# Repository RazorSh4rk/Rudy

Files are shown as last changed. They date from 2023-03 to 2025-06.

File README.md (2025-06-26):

# Rudy

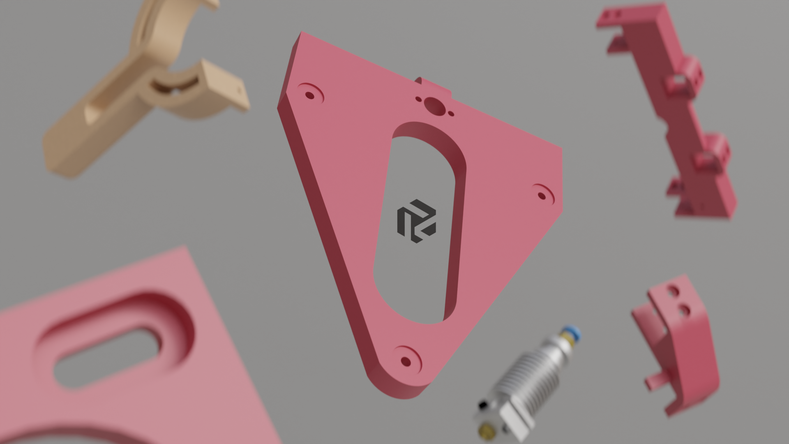
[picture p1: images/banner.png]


## What this _is_

It's a coreXY 3d printer that is

  - cheap
  - reliable
  - small
  - easy to build
  - easy to understand
  - easy to modify
  - open frame

## What this _ain't_

- The fastest printer in the west

- A zero compromise machine

- Something off the shelf

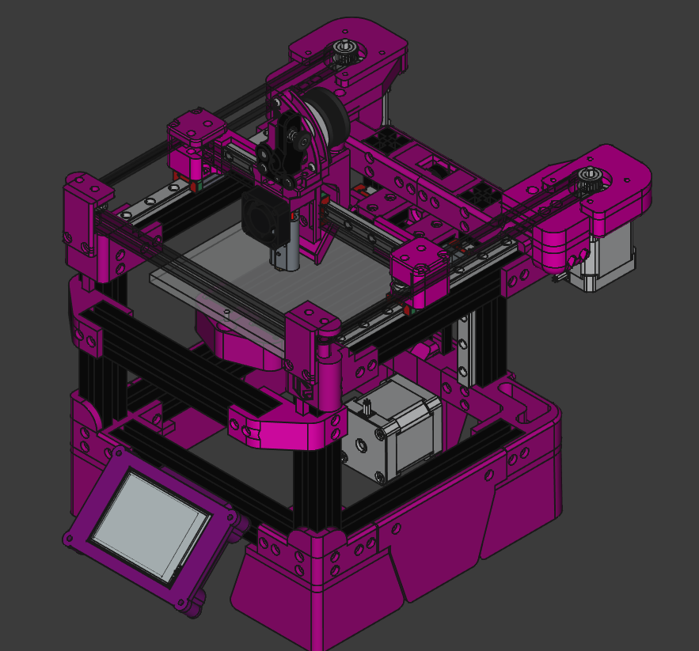
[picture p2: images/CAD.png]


<a href="https://www.youtube.com/watch?v=9IVwhJpB8qE">
    See it in action
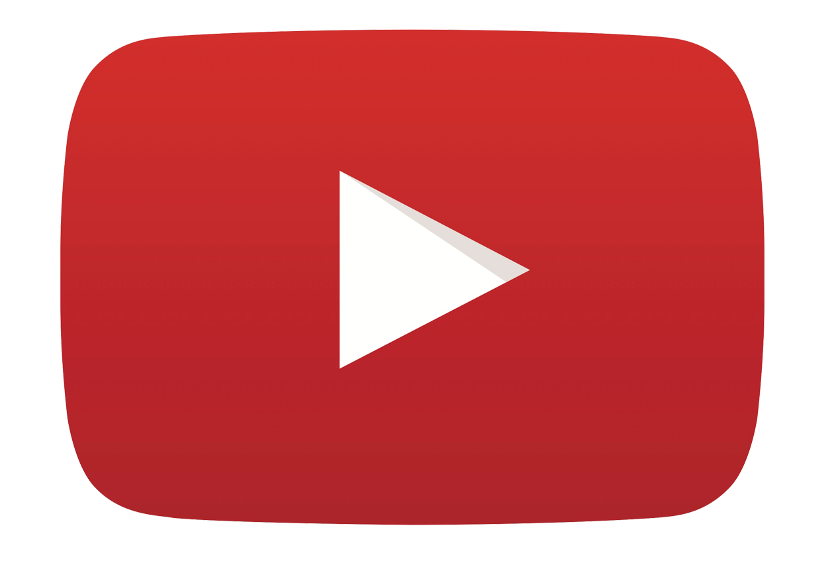
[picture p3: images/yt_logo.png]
    
</a>

<a href="https://discord.com/invite/MBcHGUv2CB">
    Join the discord
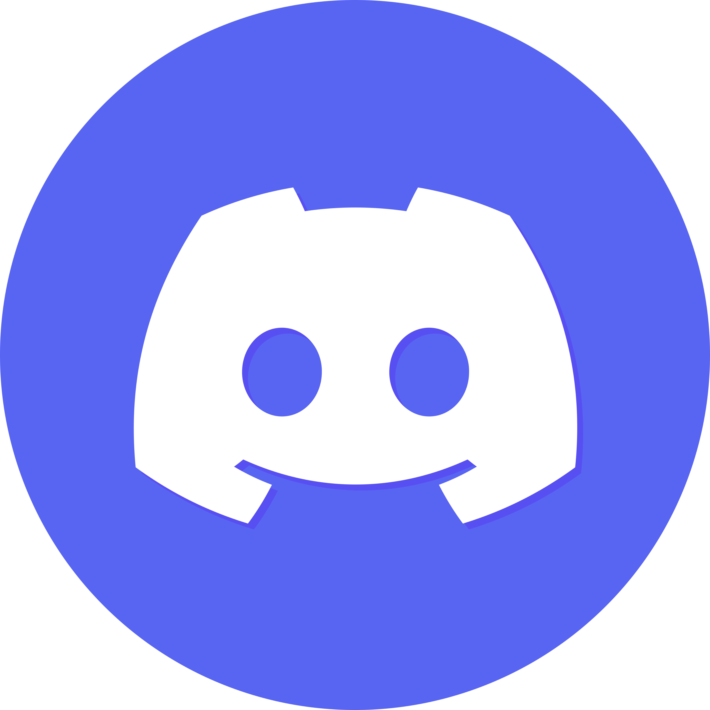
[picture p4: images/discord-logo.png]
    
</a>

---

## GUIDES

 - [Sourcing the parts](./SOURCING_GUIDE.md)
 - [Printing the files](./PRINTING_GUIDE.md)
 - [Choosing a toolhead](./TOOLHEAD.md)
 - [Assembly](./build_guide/assembly.md)

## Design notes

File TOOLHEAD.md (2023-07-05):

# Choosing a toolhead

Rudy uses a front facing mgn9c carriage, so any toolhead that supports that
should work. You ideally want something that's as small on x and y as possible
to not limit travel. If you are using limit switches, you also want to make sure that your toolhead can hit those. 

## Warhead

The Warhead is a custom design specifically made for Rudy. It uses a V6 hotend
with a 3010 fan and a 4010 blower for part cooling. Since it's not strictly a 
part of the Rudy project, it has its own repository and BOM, but if you purchace
the Rudy BOM, you should have enough leftovers to build it too.

Pros:

    - tiny, barely bigger than a V6
    - prints quickly
    - uses standard parts

Cons:

    - in active development
    - the part cooling is okay at best, this is being worked on

[Warhead](https://github.com/RazorSh4rk/warhead)

## Rookery

The Rookery is a very well designed toolhead from Gulsifer on the Rook discord.
It uses the same mounting style as Rudy so it should work too.

Pros:
    
    - much more mature design
    - supports different hotends

Cons:

    - default hardware is very weird, it uses both MK8 and Volcano parts
    - slightly more expensive to source
    - I personally am not convinced of its hotend cooling capability
    - big, it will limit x and z travel

[Rookery](https://www.printables.com/model/381953-rookery-bowden-tool-head)

## DDRudy

DDRudy is a direct drive toolhead custom-designed for the Rudy printer by @skillenmcnot. It is based off the Orbiter v2 extruder and the Trianglelabs CHC Mini hotend.
Other hotend and extruder combinations are possible, although a different extruder may require moving the mounting hole positions in the model.

Pros:
    
    - custom designed for Rudy
    - supports different hotends and common replacement parts
    - excellent cooling performance
    - actively being improved
    - editable model files available

Cons:

    - requires a moderately well-calibrated machine to print properly
    - wider than Warhead, it will limit x travel to 90mm

[DDRudy](https://github.com/skillenmcnot/DDRudy)

# Salad fork

The Salad fork uses the same rail for x, and the modified the mini afterburner
and the mini stealthburner from the voron 0 to fit that. While this is currently
not officially supported on Rudy, i don't see any reason why it couldn't be 
used.

[Salad fork](https://github.com/PrintersForAnts/Salad_Fork/tree/master/STL/Toolhead)

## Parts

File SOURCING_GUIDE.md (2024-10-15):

# BOM

__IMPORTANT__ Rudy was designed with aliexpress in mind. This means that a lot of unevenness, slop, and general China quality is already factored into the printed parts. The frame uses flextures to guarantee squareness, even if the metal parts are bent. Feel free to go for the cheapest listings you can find, or even print parts of the frame yourself (2020 beams are prime candidate for this).

# Frame

| 2020 length | pieces | for what |
| --- | --- | --- |
| 150mm | 6 | top and bottom squares |
| 150mm | 2 | bed carriage | 
| pick a length | 4 | frame Z |

# Z

### for all configs: 

The length of the Z rails is going to be the length of your Z 2020 extrusions _MINUS 50mm_, so if you picked 200mm, then your rails are 150mm, which will give you about 120mm travel.

| Thing | Price | Link |
| --- | --- | --- |
| mgn9c rail (Z length) x2 | - | keep scrolling |

### for leadscrew config:

| Thing | Price | Link |
| --- | --- | --- |
| T8 leadscrew (Z length) P:2mm L:8mm| $2.50 | [link](https://www.aliexpress.com/item/1005002277808736.html?spm=a2g0o.cart.0.0.5c4138daTHlXeg&mp=1) |
| 5x8mm coupler * | $1 | [link](https://www.aliexpress.com/item/32693571252.html?spm=a2g0o.order_detail.order_detail_item.3.2ce7f19cw1xHpY) |

### for belted Z config:

| Thing | Price | Link |
| --- | --- | --- |
| extra belt (3m will have leftover for about 120mm Z) | | |
| extra F695 x2 (there will be enough leftovers) | | |
| one extra gt2 pulley | | keep scrolling |
| M5x35 screw (x40 works too, it will just stick out) | | keep scrolling |

# Common parts

| Thing | Price | Link |
| --- | --- | --- |
| __Hardware__ | | |
| M3 sliding T-nuts x200 (2020 series) | $9 | [link](https://www.aliexpress.com/item/1005002114332413.html?spm=a2g0o.productlist.main.5.3641402fC0BsdY) |
| M3x6 metric screws x200 |  |  |
| M3x8 metric screws x50 (for backup or accessories) |  |  |
| M3x25 (or longer) metric screws x3 |  |  |
| M3x20 x10 |  |  |
| M3x something between 10 and 20 x2 |  |  |
| M2x10 metric screws x2 (optional, hot glue is fine) |  |  |
| M5x40 metric screws x10 |  |  |
| M5 hex nut x2 |  |  |
| M3 (XD5.0XL4.0) inserts x100 (you need 20) | $7.34 | [link](https://www.aliexpress.com/item/4000232858343.html?spm=a2g0o.order_list.order_list_main.107.21ef1802qkslow) |
| __Motion__ |  |  |
| GT2 pulley x2 * | $6.34 | [link](https://www.aliexpress.com/item/32995102911.html?spm=a2g0o.order_list.order_list_main.107.145f1802vFsakT) |
| 6mm GT2 belt x3m | $7.61 | [link](https://www.aliexpress.com/item/902692789.html?spm=a2g0o.order_list.order_list_main.108.145f1802vFsakT) |
| F695 bearing x20 | $23 | [link](https://www.aliexpress.com/item/33001186278.html?spm=a2g0o.order_list.order_list_main.97.145f1802vFsakT) |
| Cheaper F695 (they work fine) | $11 | [link](https://www.aliexpress.com/item/1005004095001000.html) |
| mgn9c rail 150mm x3 * | $30 | [link](https://www.aliexpress.com/item/1005003787436599.html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) |
| 120mm voron 0 bed | $20 | [link](https://www.aliexpress.com/item/1005003229750626.html?spm=a2g0o.order_list.order_list_main.102.21ef1802qkslow) |
| 8x20mm bed springs | $2 | [link](https://www.aliexpress.com/item/1005002971412129.html?spm=a2g0o.productlist.main.1.6c086ad58K77Ue) |
| __Electronics__ |  |  |
| 3x NEMA17 | $25 | [link - pancake](https://www.aliexpress.com/item/1005004708155105.html?spm=a2g0o.order_list.order_list_main.102.145f1802vFsakT) |
| other motor listing (cheaper if you wanna buy 5) | $38 | [link](https://www.aliexpress.com/item/1005001650755939.html?spm=a2g0o.cart.0.0.202b38da9QMU82&mp=1)
| skr pico (or any tmc2209 mainboard) | $20-30 | [pico](https://www.aliexpress.com/item/1005004046648820.html?spm=a2g0o.productlist.main.3.3697bf5bSHKD6H)|
| Orange Pi Zero 2 (or something to run klipper) | $30 | [link](https://www.aliexpress.com/item/1005001823662622.html?spm=a2g0o.productlist.main.1.3a4a1cacYamf5s) |
| Limit switch x1 (MS-1A 13.5) | $1.50 | [link](https://www.aliexpress.com/item/4001033375208.html?) |
| Power supply 24V (~120W) | $20-30 | [link](https://www.aliexpress.com/item/1005004623323483.html?spm=a2g0o.cart.0.0.64b338dahPVvNM&mp=1) |
| Extruder (titan or bmg recommended) | $5-10 | [titan link](https://www.aliexpress.com/item/10000404181488.html?spm=a2g0o.productlist.main.29.219338f9jwvYx4) |

### Extruder notes

If you use bowden, just use whatever extruder you like, a voron m4 or a bmg clone is nice and cheap.

If you want to go bowden, warhead has support for sailfin, and will eventually have support for sherpa micro, so pick either of those (sailfin can be built from a $5 bmg kit)

// BOM subject to change

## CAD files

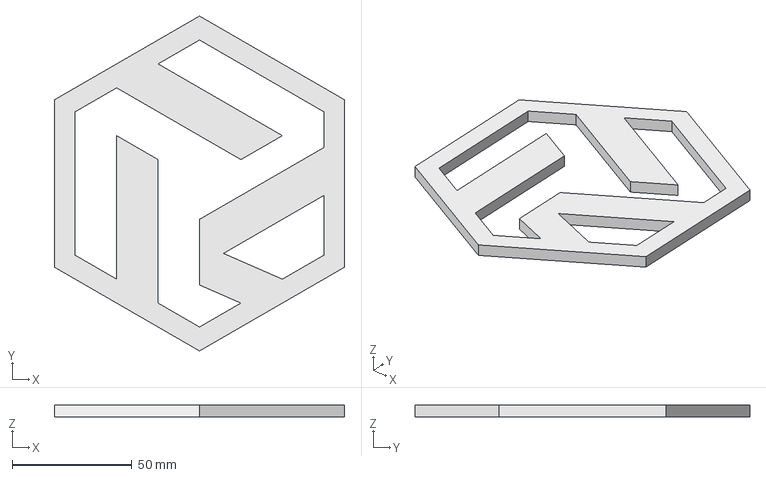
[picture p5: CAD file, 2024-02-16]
logo.step
121.2 x 140.0 x 5.00 mm

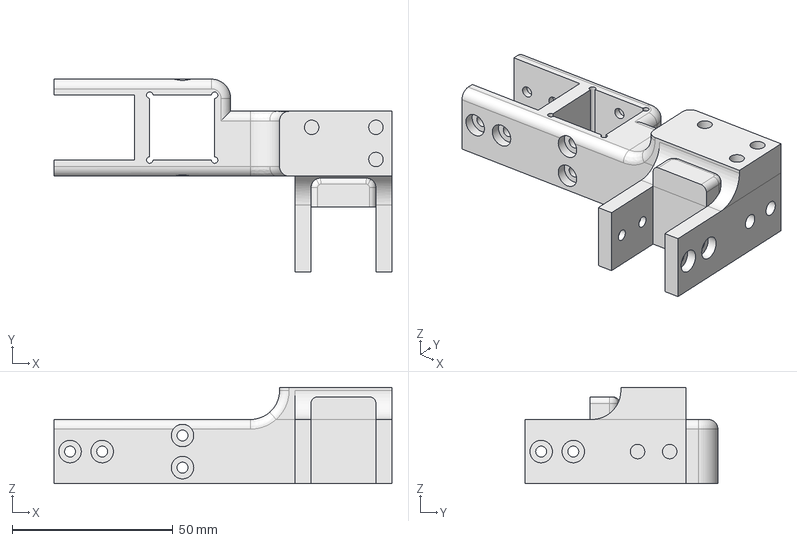
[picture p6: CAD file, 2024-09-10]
refparts/CAD_RR-back_top_right.step
105.2 x 60.0 x 30.0 mm

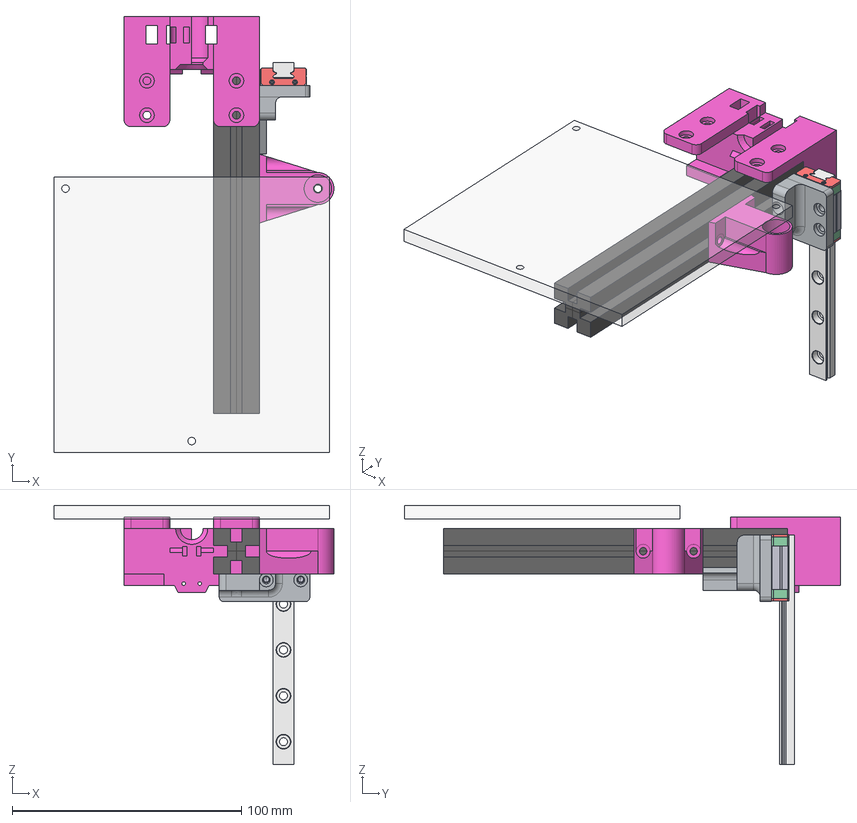
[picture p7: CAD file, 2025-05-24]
STEPs/extras/klicky/reference_z.step
122.0 x 190.0 x 113.0 mm
2020_Y_5
mgn9_z1
MGN9CZFC-Block039
MGN9CZFC-Block040
MGN9CZFC-Block041
MGN9CZFC-Block042
MGN9CZFC-Block043
MGN9CZFC-Block044
MGN9CZFC-Block045
MGN9CZFC-Block046
MGN9CZFC-Block047
Z_reprap_right
Z_reprap_v0_right
V0_bed
Z_reprap_belt

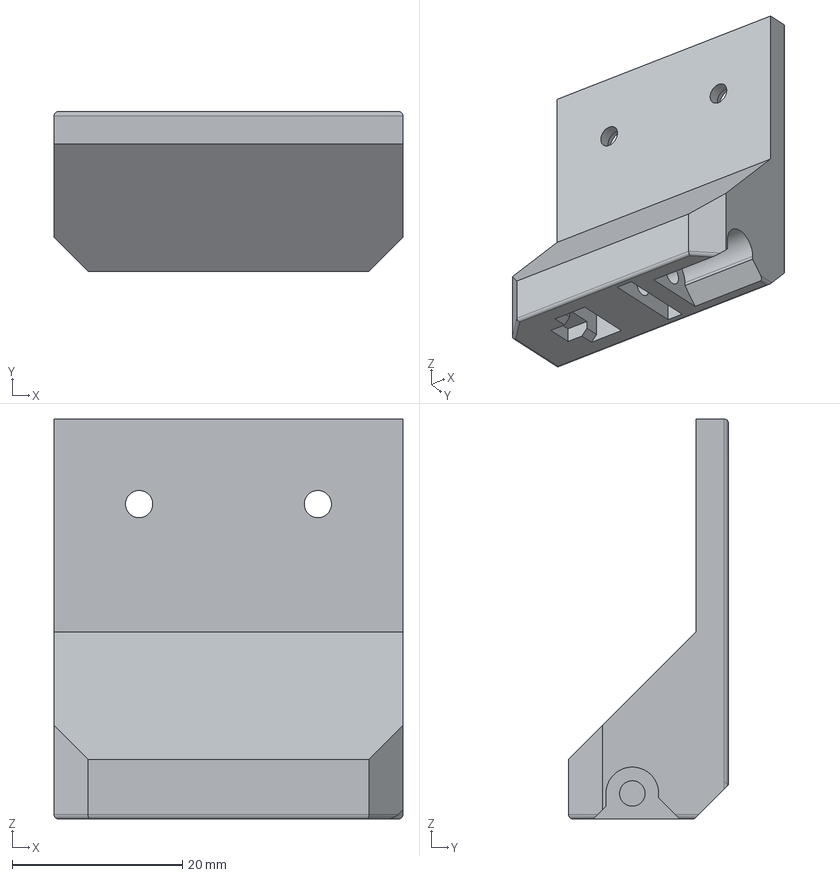
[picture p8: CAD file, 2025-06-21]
STEPs/extras/klicky/sideswipe/servo_mount.step
41.0 x 18.8 x 47.0 mm

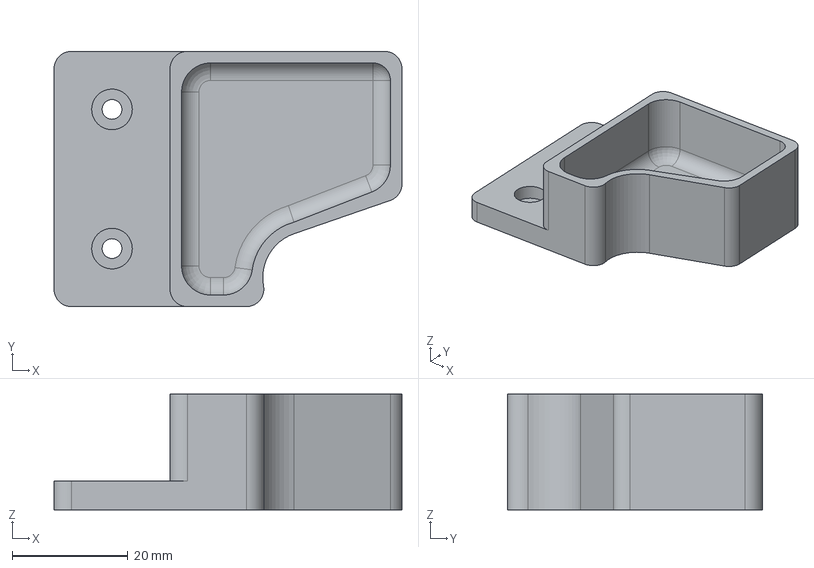
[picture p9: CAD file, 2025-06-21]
STEPs/extras/purge_bucket.step
60.0 x 44.0 x 20.0 mm

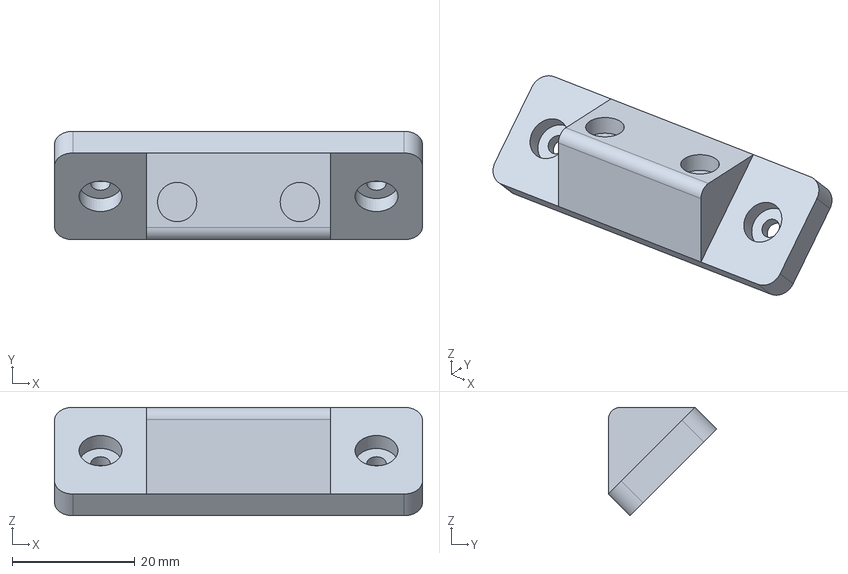
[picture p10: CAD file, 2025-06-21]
STEPs/extras/screen/mount.step
60.0 x 17.7 x 17.7 mm

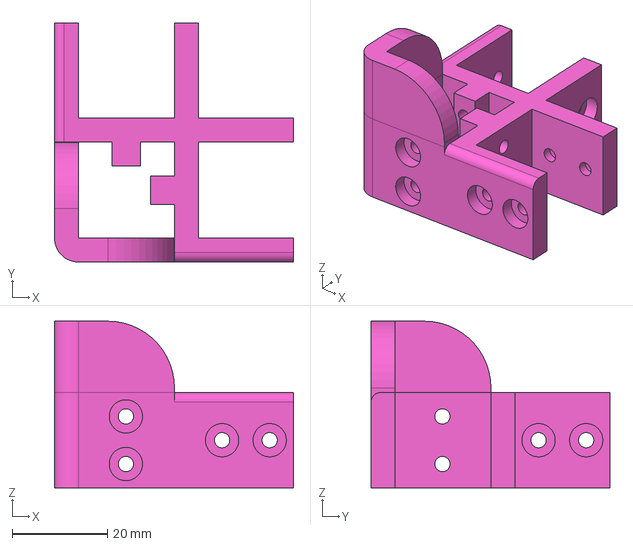
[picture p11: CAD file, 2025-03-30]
STEPs/MK4/frame/bottom/corner_x2.step
50.2 x 50.2 x 35.0 mm

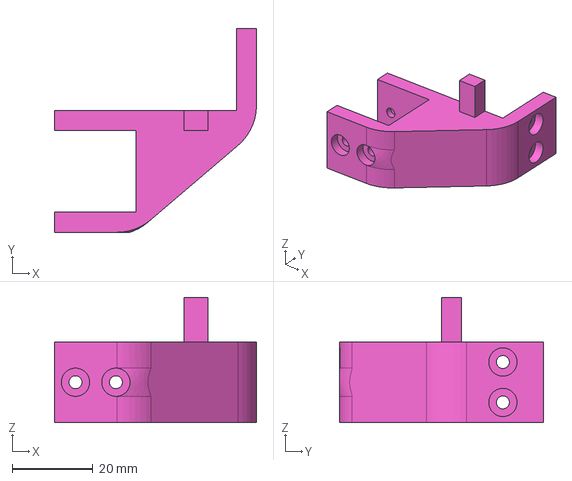
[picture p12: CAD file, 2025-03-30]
STEPs/MK4/frame/top/front_bar_right.step
50.0 x 50.4 x 31.0 mm

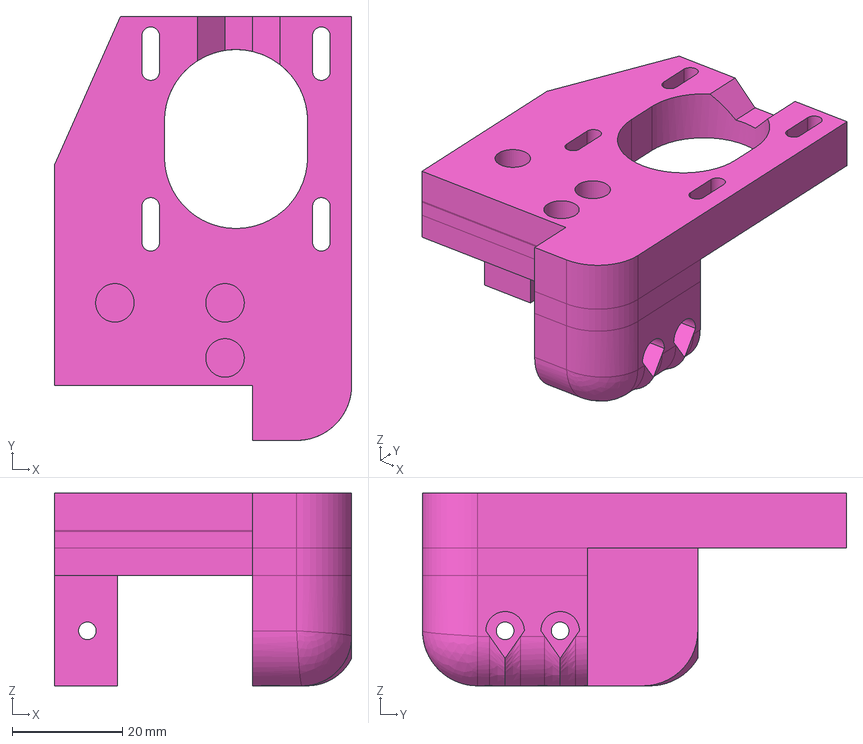
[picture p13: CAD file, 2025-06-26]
STEPs/MK4/motion/XY/motor_mount_right.step
54.0 x 77.0 x 35.0 mm

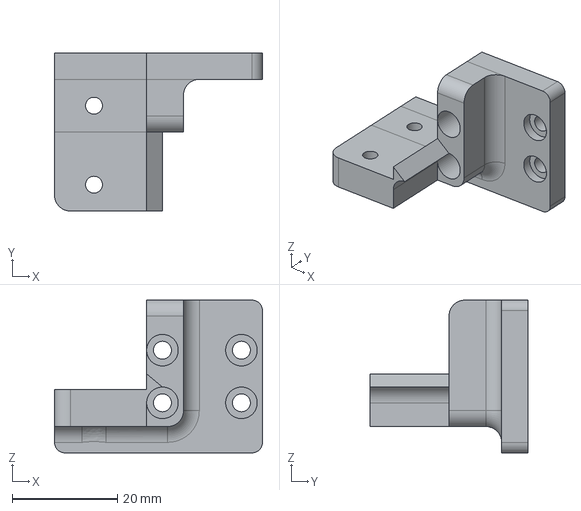
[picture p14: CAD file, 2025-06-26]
STEPs/MK4/motion/Z/bed_carriage_rail_mount_right.step
39.5 x 30.0 x 29.0 mm

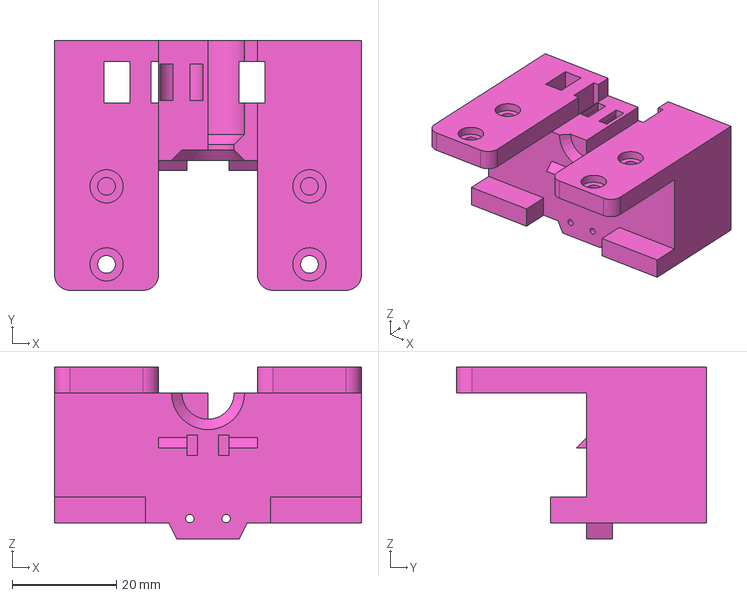
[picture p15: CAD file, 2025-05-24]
STEPs/MK4/motion/Z/belted/belt_attachment.step
59.0 x 48.0 x 33.0 mm

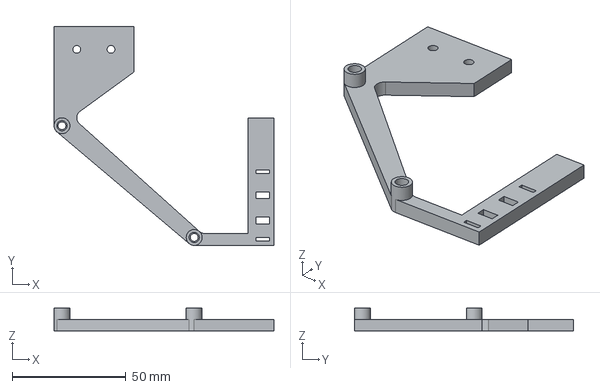
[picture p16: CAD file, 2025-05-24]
STEPs/MK4/mount_stuff/skrpico_mount.step
96.5 x 96.0 x 10.0 mm

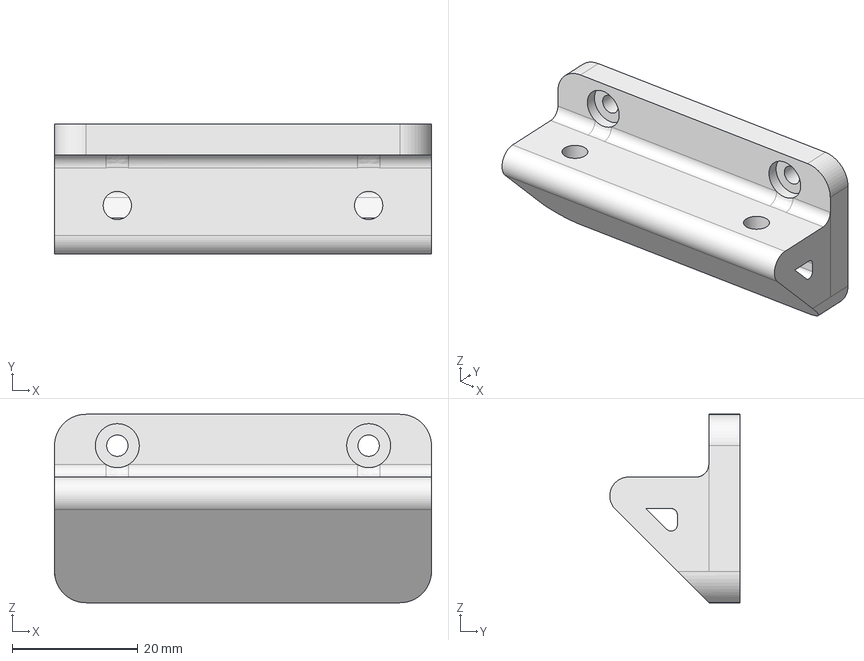
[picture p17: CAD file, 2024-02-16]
STEPs/spool_holder/spool_holder-base.step
60.0 x 20.8 x 30.0 mm

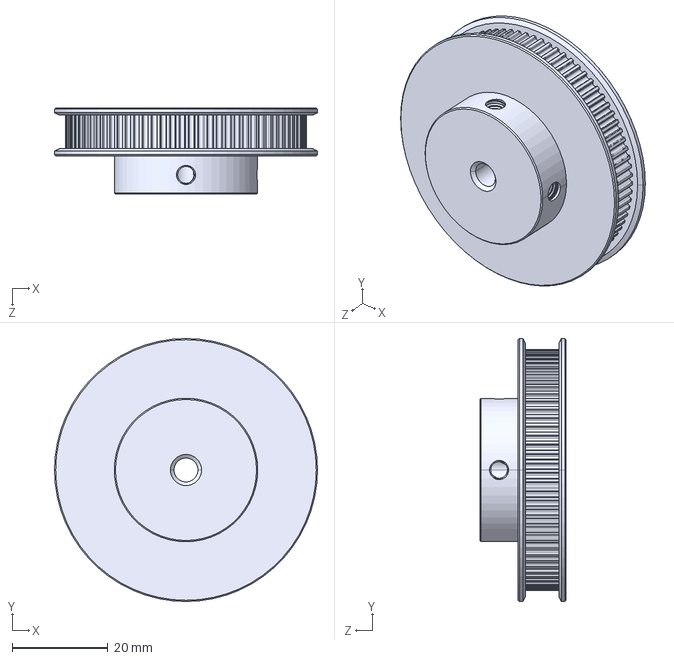
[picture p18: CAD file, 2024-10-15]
things_i_used_for_reference/GT2_80T_5mm_Bore_Pulley.STEP
55.0 x 55.0 x 18.0 mm

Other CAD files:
bed_model_SS.stl
refparts/CAD_RR-back_top_left.step
STEPs/extras/klicky/klicky_cad.FCStd
STEPs/extras/purge_bucket_tall.step
STEPs/MK4/frame/bottom/foot_front_left.step
STEPs/MK4/frame/bottom/foot_front_right.step
STEPs/MK4/frame/bottom/foot_rear_left.step
STEPs/MK4/frame/bottom/foot_rear_right.step
STEPs/MK4/frame/bottom/rear_left.step
STEPs/MK4/frame/bottom/rear_right.step
STEPs/MK4/frame/bottom/skirt_x2_or_x3.step
STEPs/MK4/frame/top/font_bar_left.step
STEPs/MK4/frame/top/front_corner_left.step
STEPs/MK4/frame/top/front_corner_right.step
STEPs/MK4/frame/top/rear_corner_left.step
STEPs/MK4/frame/top/rear_corner_right.step
STEPs/MK4/motion/XY/YCarriage_bottom_left.step
STEPs/MK4/motion/XY/YCarriage_bottom_right.step
STEPs/MK4/motion/XY/YCarriage_top_left.step
STEPs/MK4/motion/XY/YCarriage_top_right.step
STEPs/MK4/motion/XY/belt_tensioner_left.step
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

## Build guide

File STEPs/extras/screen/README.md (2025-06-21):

Uses a 2.8" CYD screen to add a control interface for like $10

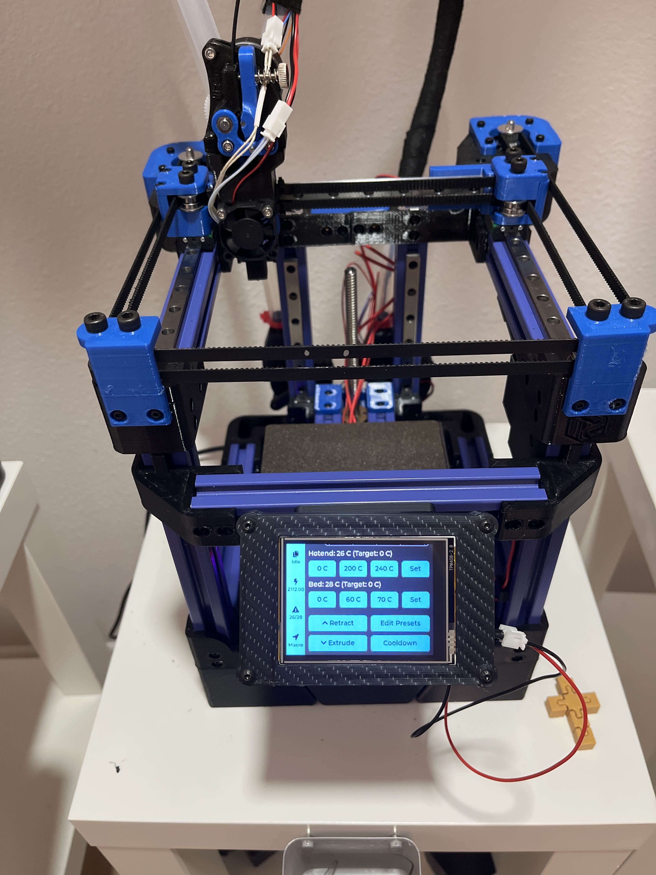
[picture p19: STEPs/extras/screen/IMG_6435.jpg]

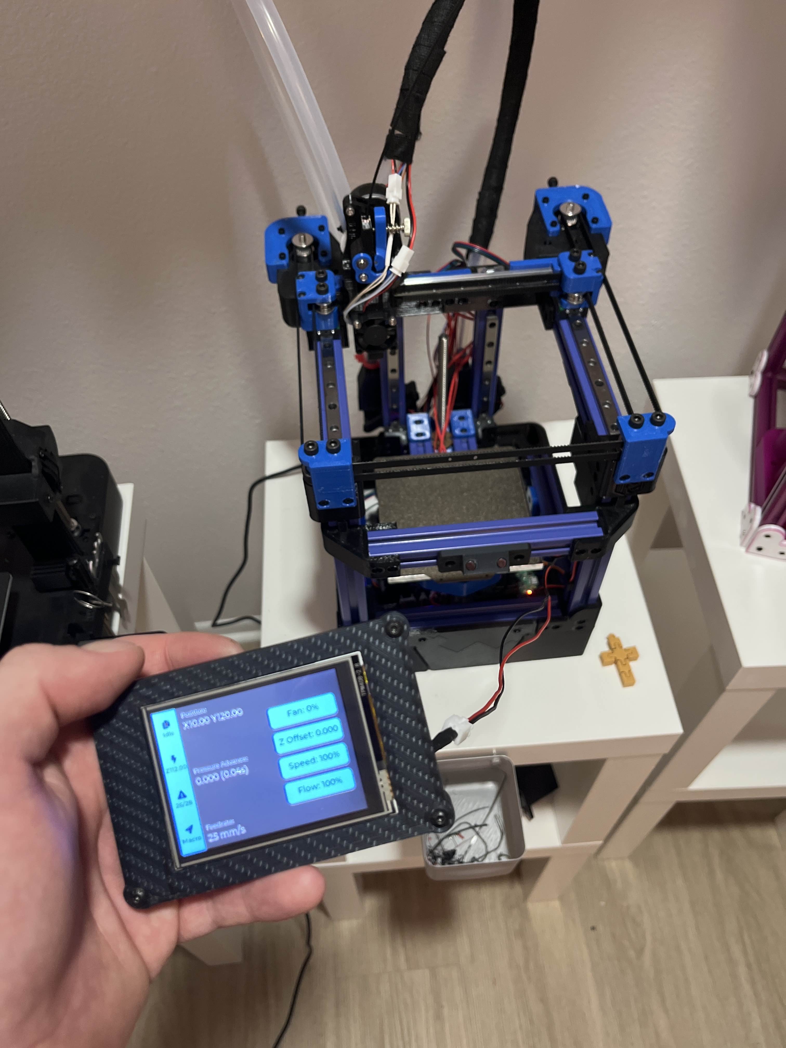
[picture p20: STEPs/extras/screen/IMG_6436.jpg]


Installation: [CYD Klipper](https://github.com/suchmememanyskill/CYD-Klipper)

BOM:

- 5mm OD heated insert x7
- M3x6mm x5
- M3x8? mm x4
- M3 2020 nut x2
- 2.8" CYD (link in the CYD Klipper repo)
- 6x3mm magnet x4

Assembly:

- Flash CYD Klipper
- Add heated inserts to the very obvious holes
- Glue magnets in mount and base
- Supply 5v to the CYD, I used one of the endstop ports, but you can also just use USB

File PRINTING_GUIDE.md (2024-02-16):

# Printing the parts

## Material

Rudy is designed to be easy to print. I used Devil Design PETG for every part. I can't really vouch for PLA working or not, but looking at the design it should be fine for everything but the AB motor mounts. ABS and nylon will most likely work. 

## Slicer

I use superslicer (analogous to prusaslicer), so I can only help with those. If you use cura or simplify3d or whatever, you probably know way more about it than I do anyway.

## Settings

Every part should be printed at 5mm solid walls. This means that if your wall thickness is 1mm, use 5 walls. If it's .8mm (common with .4 nozzles), use 5/.8 = 6.25 (6 or 7) walls. In superslicer you can set this at print settings/vertical_shells. Infill doesn't really matter, i used 18% gyroid. 

Some parts _will_ need suports turned on to make the CAD simpler. Generally "supports on build plate only" should get you most of the way there except the Y carriages where you will need paint-on, or tree support (more on that later).

Every part has a flat surface you can print it on.

## Printing the trickier parts

There are some parts that will need you to tweak settings a bit. Most notorious is gonna be the Y carriages. Use this image to paint on the supports.

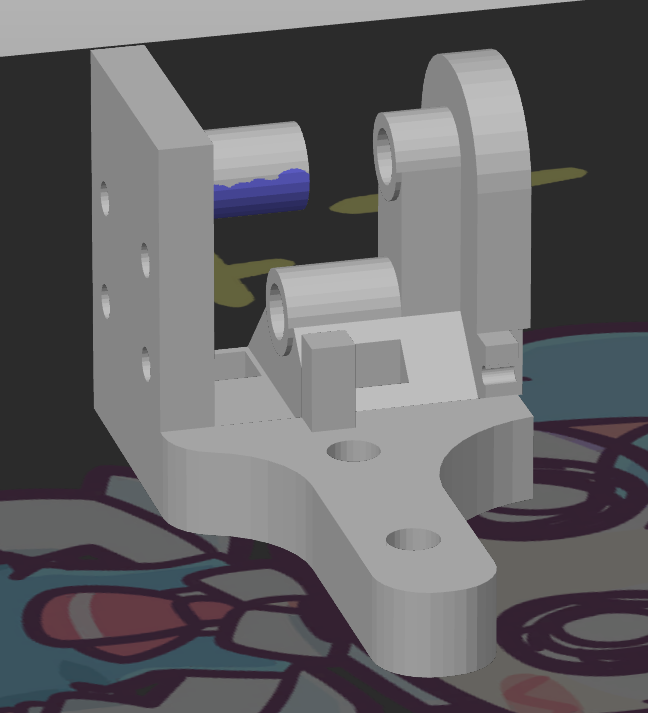
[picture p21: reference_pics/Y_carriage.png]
y


For every other part you want the counterholes to be supported so they don't sag (especially if printing PETG)

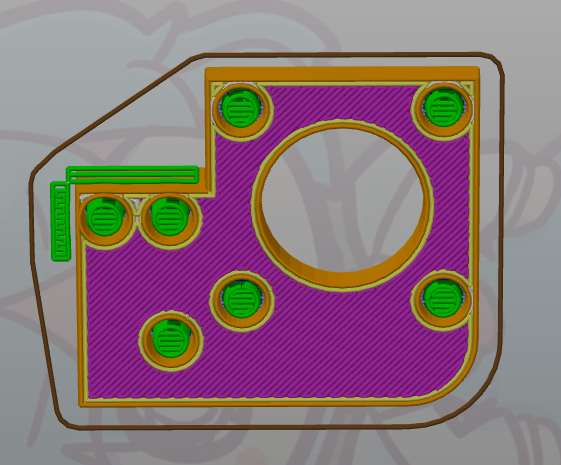
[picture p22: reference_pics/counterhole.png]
support


## Part list

### SCROLL DOWN FOR UPDATED MK2 AND MK3 PARTS

Some parts you will have to mirror in your slicer. To do this in superslicer, right click the imported stl and click "mirror/along X axis". Only place the flat sides down after.

| file | pieces | second one mirrored? |
| --- | --- | --- |
| mgn9_mount_100mm.stl | 2 | no |
| mgn9_mount_150mm.stl | 2 | no |
| back_bottom.stl | 1 |  |
| back_top.stl | 1 |  |
| bed_frame.stl | 1 |  |
| bottom_corner.stl | 2 | no |
| foot_front.stl | 2 | yes |
| `^one mirrored only if you want the logo on the other side` |  |  |
| front_bar_mount.stl | 2 | yes |
| idlerv2-right.stl | 1 | mirror this part!! |
| idlerv2.stl | 1 |  |
| leg_back.stl | 2 | yes |
| motor_mount_A.stl | 2 | yes |
| motor_mount_B_spacer.stl | 1 |  |
| skirt.stl | 3 | no |
| spool_holder.stl | 1 |  |
| top_corner.stl | 2 | no |
| y_carriage_left (Mirror #1).stl | 1 |  |
| y_carriage.stl | 1 |  |
| foot_left_logo.stl | 1 |  |
| leveling_knob.stl | 3/4 | no |
| limit_switch_spacer.stl | 2 | no |
| logo_insert.stl | 1 |  |
| mgn_rail_stopper.stl | 2 | no |

## Part list for MK2

| file change | pieces | second mirrored? |
| --- | --- | --- |
| idlerv2-right.stl -> MK2/idlerv3_right.step| 1 |  |
| idlerv2.stl -> MK2/idlerv3_left.step| 1 |  |
| motor_mount_A.stl -> MK2/motor_mount_left.step | 2 | yes |
| top_corner.stl -> not needed|  |  |
| y_carriage_left -> MK2/y_carriage_v2.step | 1 |  |
| y_carriage.stl -> MK2/y_carriage_v2_right_mirrored.step | 1 |  |
| NEW PARTS |  |  |
| MK2/belt_tensioner_left.step | 2 | yes |

## Part list for MK3

| file change | pieces | second mirrored? |
| --- | --- | --- |
| bed_frame.stl -> not needed |  |  |
| NEW PARTS |  |  |
| MK3/Z_reprap_screw.step | 1 |  |
| MK3/Z_reprap_left.step | 2 | yes |
| MK3/Z_reprap_v0_front | 1 |  |
| MK3/Z_reprap_v0_side | 2 | no |

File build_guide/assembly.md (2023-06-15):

# Assembly

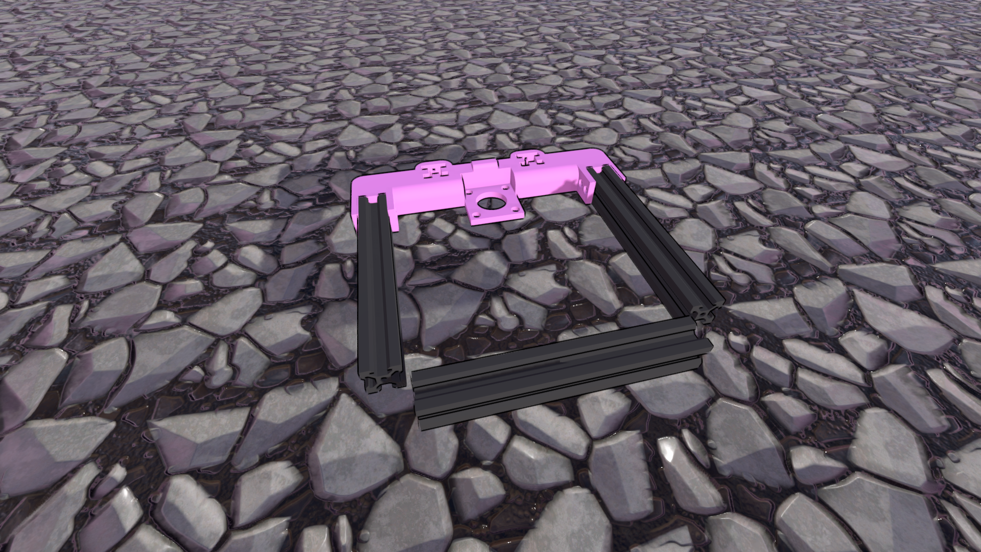
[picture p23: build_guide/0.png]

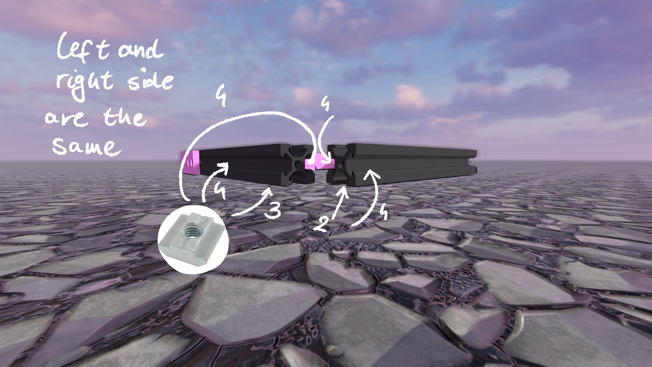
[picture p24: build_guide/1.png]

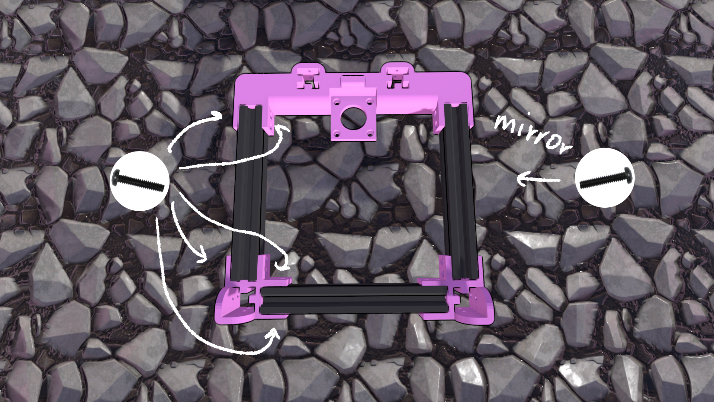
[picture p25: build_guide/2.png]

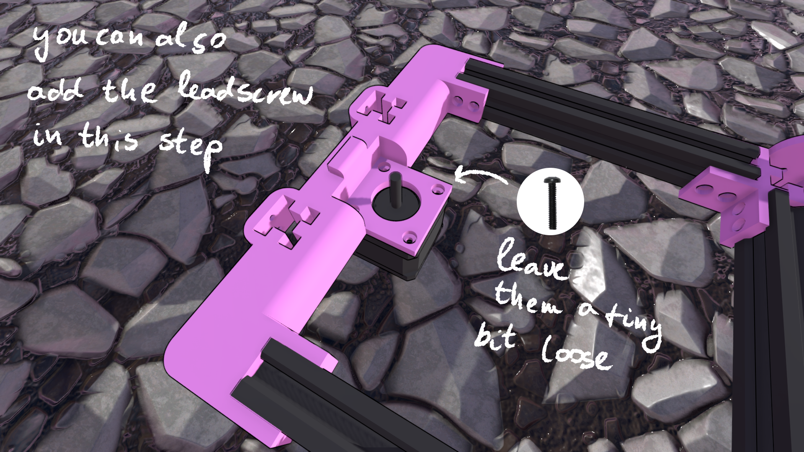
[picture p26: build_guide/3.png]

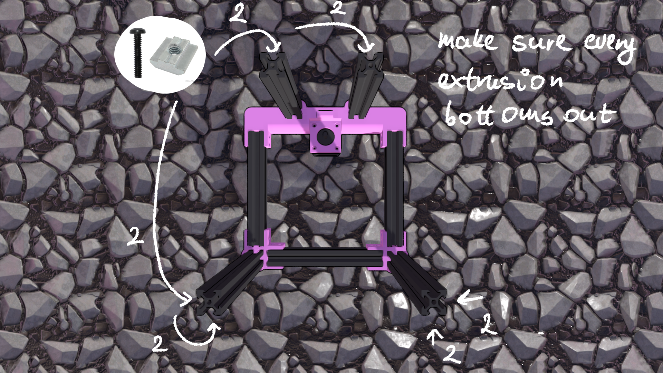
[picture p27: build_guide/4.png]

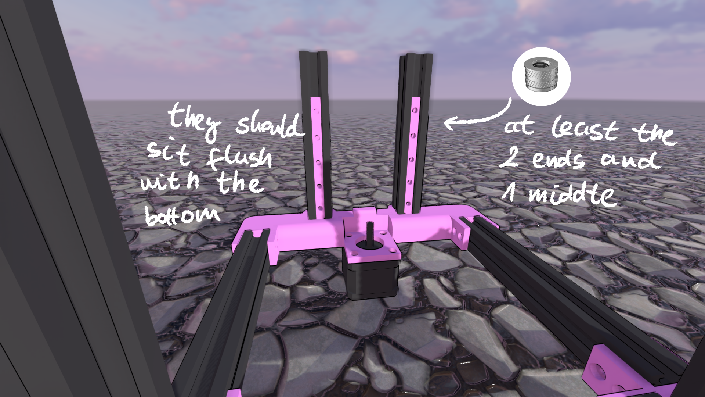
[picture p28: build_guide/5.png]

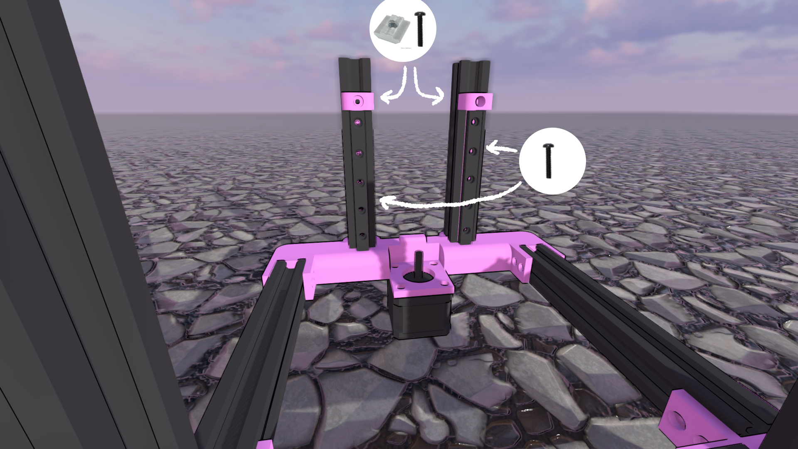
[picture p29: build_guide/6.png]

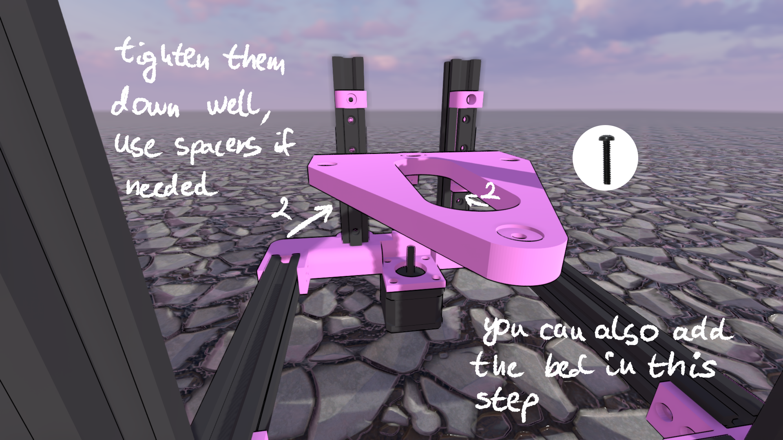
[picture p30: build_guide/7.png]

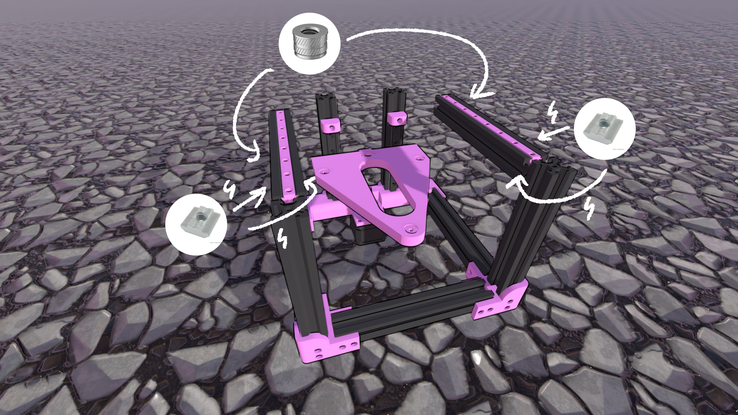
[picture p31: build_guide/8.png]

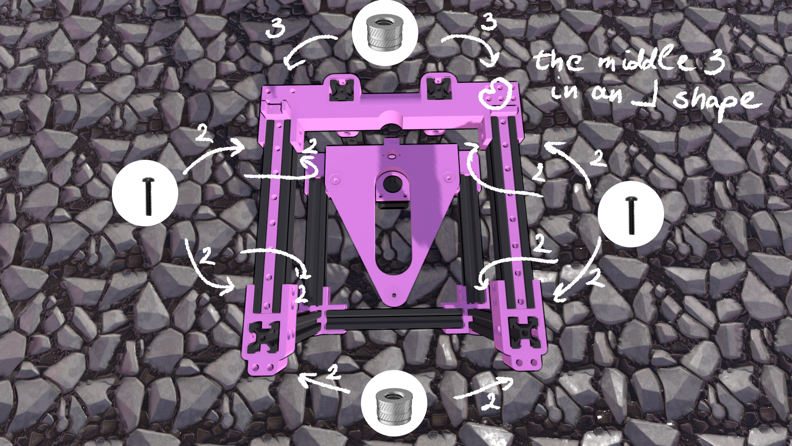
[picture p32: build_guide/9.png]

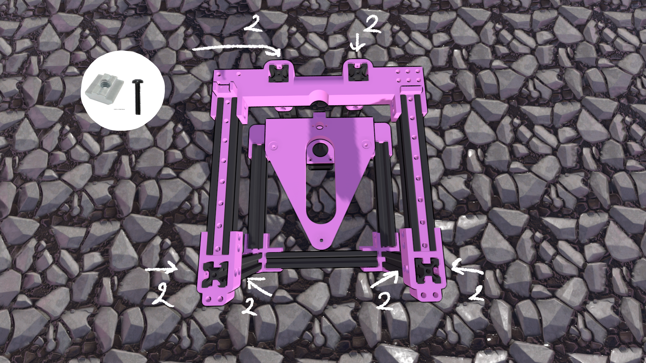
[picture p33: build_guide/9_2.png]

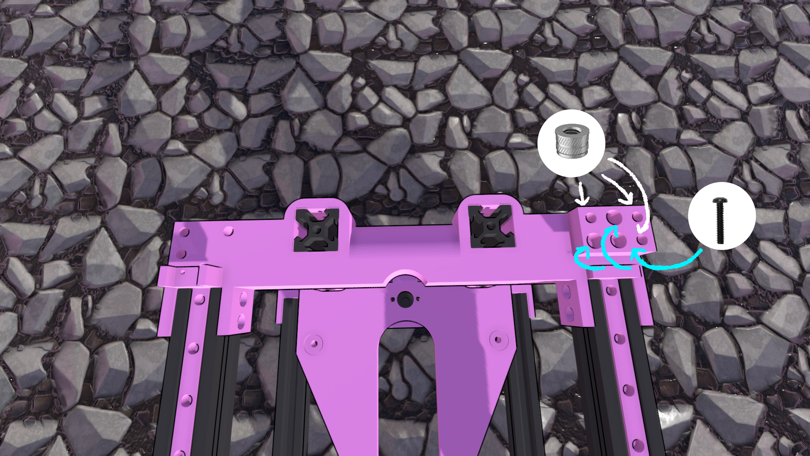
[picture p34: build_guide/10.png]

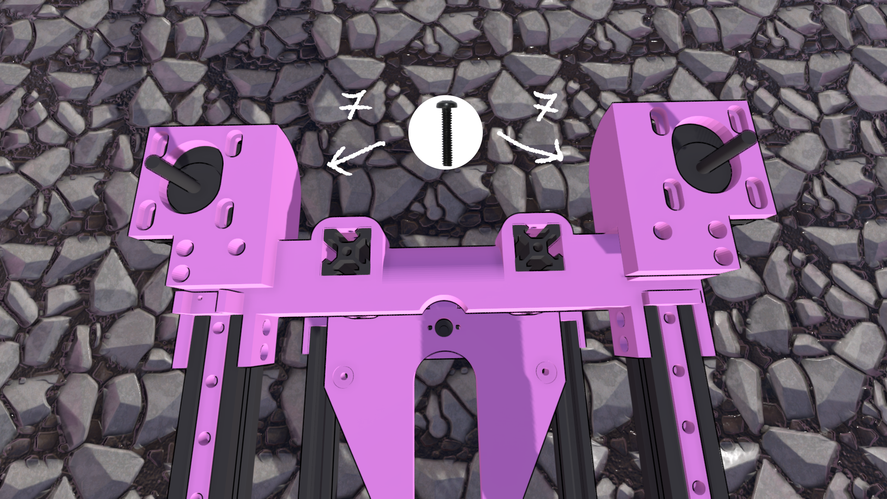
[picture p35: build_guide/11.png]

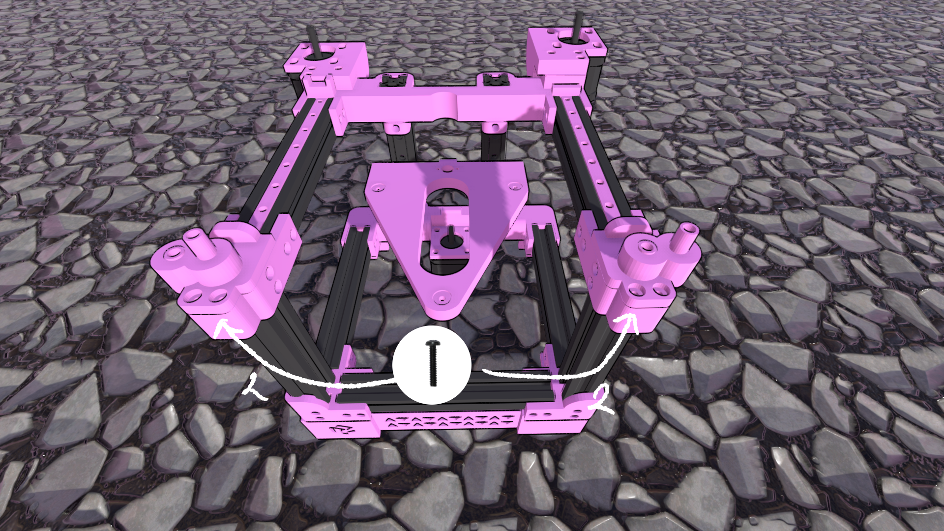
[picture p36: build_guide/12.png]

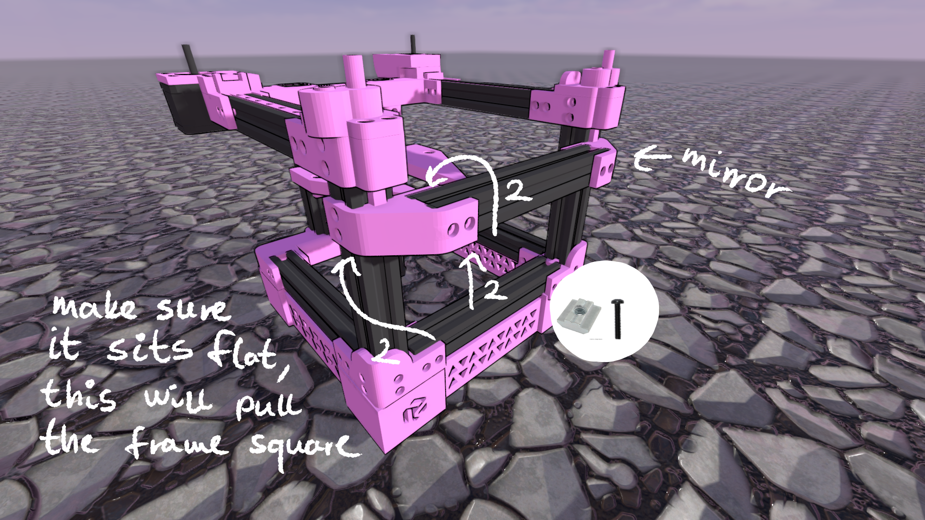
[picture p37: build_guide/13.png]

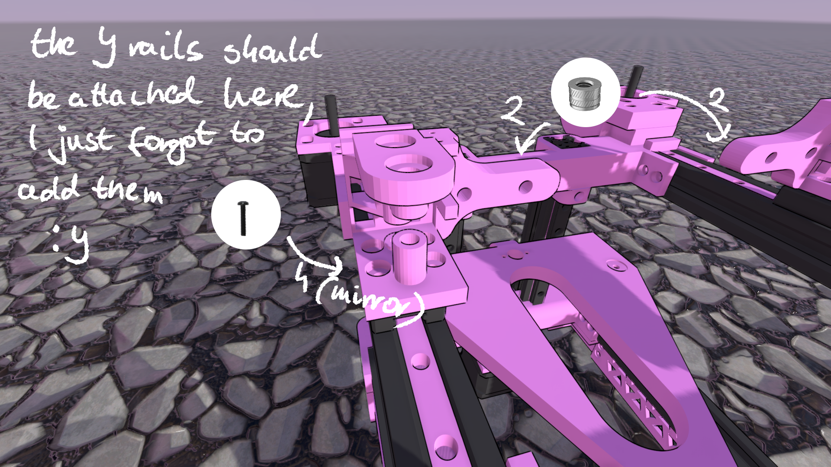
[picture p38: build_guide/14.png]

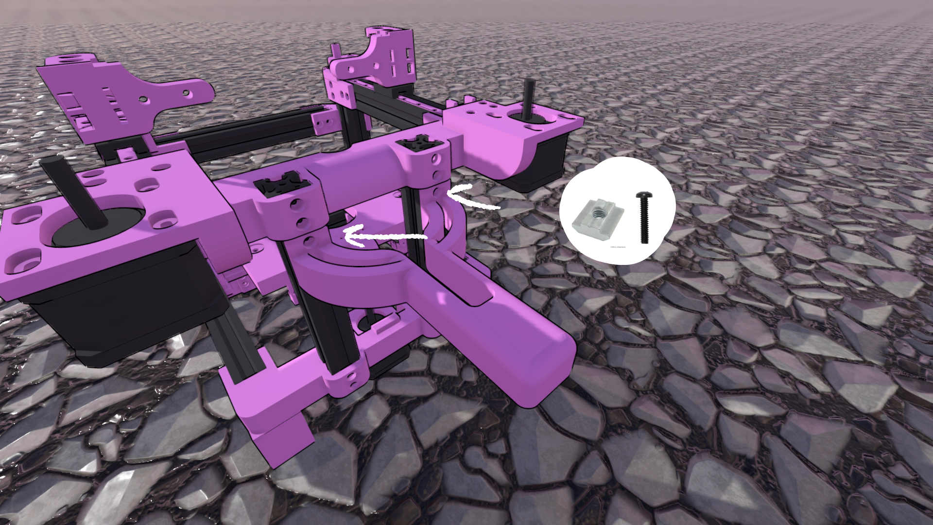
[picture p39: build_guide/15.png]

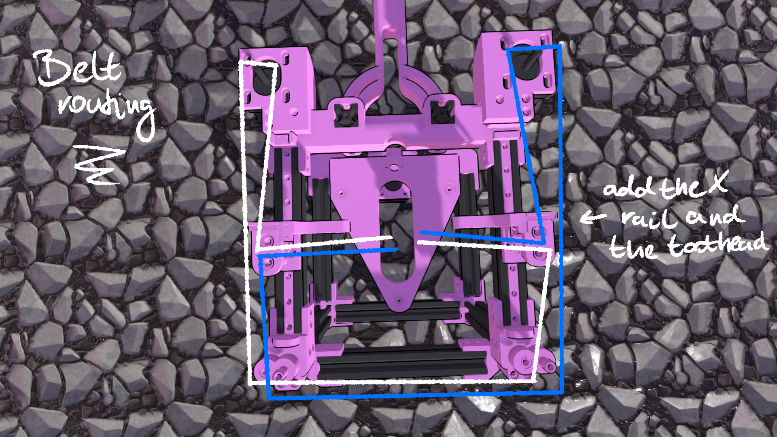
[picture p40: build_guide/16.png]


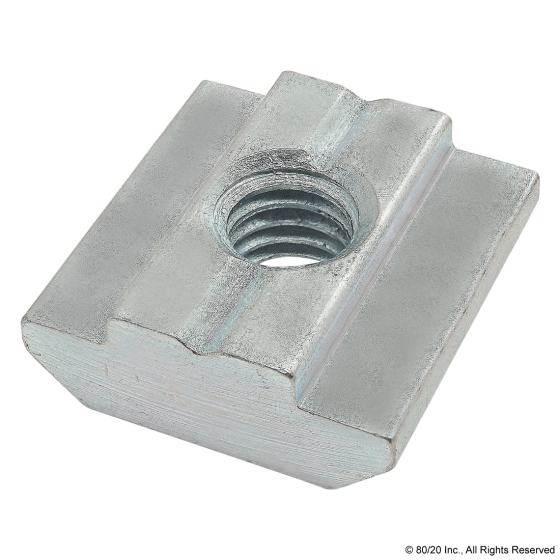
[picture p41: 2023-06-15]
build_guide/nut.png

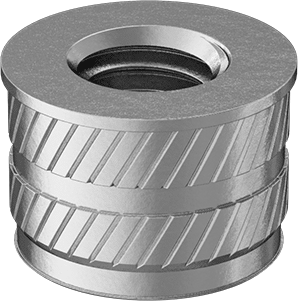
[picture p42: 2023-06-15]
build_guide/insert.png

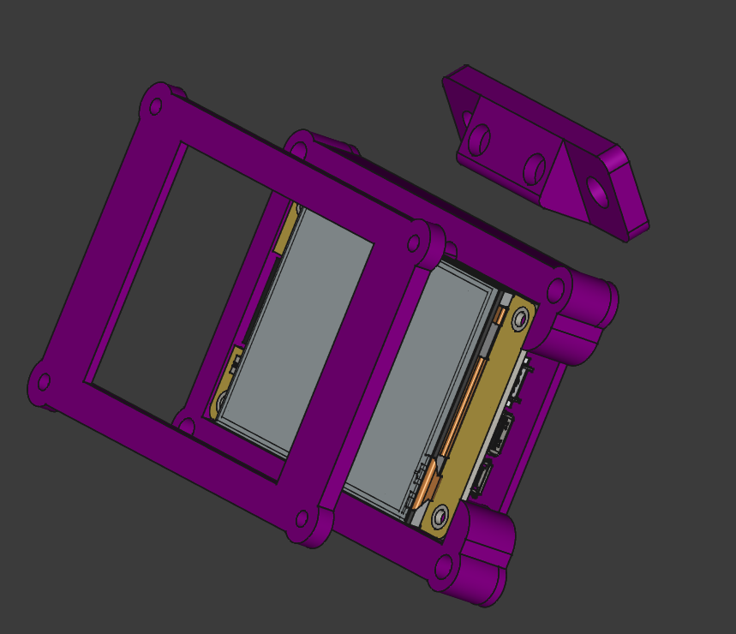
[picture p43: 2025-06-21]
STEPs/extras/screen/2025-06-21_15-06.png

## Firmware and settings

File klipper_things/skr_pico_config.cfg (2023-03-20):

[include kiauh_macros.cfg]
# [include coprocessor.cfg]

#[mcu]
#serial: usb-Klipper_rp2040_45503571290CD4A8-if00

[virtual_sdcard]
path: ~/gcode_files

[stepper_x]
step_pin: gpio11
dir_pin: !gpio10
enable_pin: !gpio12
microsteps: 16
rotation_distance: 40
endstop_pin: ^!gpio4
# endstop_pin: tmc2209_stepper_x:virtual_endstop
# homing_retract_dist: 0
position_endstop: 10
position_max: 150
homing_speed: 50

[tmc2209 stepper_x]
uart_pin: gpio9
tx_pin: gpio8
uart_address: 0
run_current: 0.58
hold_current: 0.4
stealthchop_threshold: 999999
diag_pin: ^gpio4
driver_SGTHRS: 100

[stepper_y]
step_pin: gpio6
dir_pin: !gpio5
enable_pin: !gpio7
microsteps: 16
rotation_distance: 40
endstop_pin: ^!gpio3
# endstop_pin: tmc2209_stepper_y:virtual_endstop
# homing_retract_dist: 0
position_min: 0
position_endstop: 10
position_max: 130
homing_speed: 50

[tmc2209 stepper_y]
uart_pin: gpio9
tx_pin: gpio8
uart_address: 2
run_current: 0.58
hold_current: 0.4
stealthchop_threshold: 999999
diag_pin: ^gpio3
driver_SGTHRS: 100

[stepper_z]
step_pin: gpio19
dir_pin: gpio28
enable_pin: !gpio2
microsteps: 16
rotation_distance: 8
endstop_pin: ^!gpio25
position_endstop: 66
# endstop_pin: tmc2209_stepper_z:virtual_endstop
position_min: 0
position_max: 66
homing_speed: 5

[tmc2209 stepper_z]
uart_pin: gpio9
tx_pin: gpio8
uart_address: 1
run_current: 0.580
hold_current: 0.500
stealthchop_threshold: 999999
diag_pin: ^gpio25
driver_SGTHRS: 100

[extruder]
step_pin: gpio14
dir_pin: !gpio13
enable_pin: !gpio15
microsteps: 16
rotation_distance: 6
# rotation_distance: 32.97 # 24 
# gear_ratio: 3:1 # titan extruder
nozzle_diameter: 0.5
filament_diameter: 1.75
heater_pin: gpio21 # gpio23
sensor_type: EPCOS 100K B57560G104F
sensor_pin: gpio27
#control: pid
#pid_Kp: 22.2
#pid_Ki: 1.08
#pid_Kd: 114
min_temp: 0
max_temp: 300
max_extrude_cross_section:2
max_extrude_only_distance: 1000
min_extrude_temp: 10
# pressure_advance: 0.32

[tmc2209 extruder]
uart_pin: gpio9
tx_pin: gpio8
uart_address: 3
run_current: 0.650
hold_current: 0.500
stealthchop_threshold: 999999

# [filament_switch_sensor runout_sensor]
# switch_pin: ^gpio16
# pause_on_runout: True

# [filament_motion_sensor smart_sensor]
# switch_pin: ^gpio16
# detection_length: 2.5

#[heater_bed]
#heater_pin: gpio23 # 21
#sensor_type: EPCOS 100K B57560G104F
#sensor_pin: gpio26
#control: pid
#pid_Kp: 54.027
#pid_Ki: 0.770
#pid_Kd: 948.182
#min_temp: 0
#max_temp: 130

[heater_fan hotend_fan]
pin: gpio18
heater: extruder
heater_temp: 45.0

[fan]
pin: gpio20
max_power: 0.5

[heater_fan spider]
pin: gpio17
heater: extruder
heater_temp: 190.0

[mcu]
serial: /dev/serial/by-id/usb-Klipper_rp2040_45503571290CD4A8-if00
# serial: /dev/ttyAMA0
restart_method: command

[printer]
kinematics: corexy
max_velocity: 200
max_accel: 12100
max_z_velocity: 5
max_z_accel: 10

#[bltouch]
#sensor_pin: gpio22
#control_pin: gpio29

[neopixel board_rgb]
pin: gpio24
chain_count: 1
color_order: GRB
initial_RED: 0.0
initial_GREEN: 0.1
initial_BLUE: 0.0

[force_move]
enable_force_move: True

[input_shaper]
shaper_freq_x: 87.6
shaper_type_x: mzv
shaper_freq_y: 64.2
shaper_type_y: mzv

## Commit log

2023-02-10 files lol
    [2020extrusionx.stl, 2020extrusiony.stl, 2020extrusionz.stl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]
2023-02-13 logo, BOM
    [2020extrusionx.stl, 2020extrusiony.stl, 2020extrusionz.stl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]
2023-02-15 bottom frame reinforcements
    [CAD_RR-back_bottom.stl, CAD_RR-bottom_corner.stl, CAD_RR-foot_front.stl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]
2023-02-16 clean up stls
    [CAD_RR-2020_mgn9_mount_100mm.stl, CAD_RR-2020_mgn9_mount_150mm.stl, CAD_RR-back_bottom.stl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]
2023-02-17 updated BOM
    [CAD_RR-foot_front.stl, CAD_RR-leg_back.stl, CAD_RR-skirt.stl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]
2023-02-18 add step assembly
2023-02-28 new idlers woo
    [3010_fan.step, 4010_blower.STEP, CAD_RR-idlerv2-right.stl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]
2023-03-01 new cad pic
2023-03-02 readying up fir first release
    [CAD_RR-bed_frame.stl, CAD_RR-front_bar_mount.stl, CAD_RR-idler.stl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]
2023-03-03 release tiiiime
    [CAD_RR-back_bottom.stl, CAD_RR-back_top.stl, CAD_RR-gt2_clamp.stl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]
2023-03-05 added printing guide
    [CAD_RR-spool_holder.stl, CAD_RR-toolhead.stl, CAD_RR-toolhead001.stl]
2023-03-07 default to .2mm tolerances
    [CAD_RR-back_bottom.stl, CAD_RR-back_top.stl, CAD_RR-bottom_corner.stl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]
2023-03-07 add prudy beam
    [PRudy_CAD-2020_extrusion_150mm.stl, PRudy_CAD.FCStd]
2023-03-08 new bottom corner
    [CAD_RR-bottom_corner.stl]
2023-03-09 fix the tensioner lol
    [CAD_RR-motor_mount_A.stl]
2023-03-09 edit the BOM
2023-03-09 add toolhead section
2023-03-11 fix the y carriage spacing issue
    [CAD_RR-y_carriage.stl, CAD_RR-y_carriage_left (Mirror #1).stl]
2023-03-13 add mods folder and spider duct
    [CAD_RR-spider_duct.stl]
2023-03-13 messed up a screw size but it still works so whatever
2023-03-17 add cheap steppers
2023-03-20 add an example skr pico cfg
    [skr_pico_config.cfg]
2023-04-04 add 150mm bed carriage
    [CAD_RR-150_bed_carriage.stl]
2023-04-06 fix top corner spacing issue
    [CAD_RR-top_corner.stl]
2023-04-08 updated step assembly
2023-04-08 added cheaper bearings to BOM
2023-04-26 mommy exported a step alriiight
    [leveling_knob_small.stl]
2023-05-06 fix a small mistake in the printing guide
2023-05-30 add switches to bom
    [CAD_RR-idlerv3.stl]
2023-07-05 add steps for every part
    [5015_bracket.stp, CAD_RR-150_bed_carriage.step, CAD_RR-2020_mgn9_mount_100mm.step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]
2023-10-24 motor mount, tensioner, front idler
    [CAD_RR-belt_tensioner_left.step, CAD_RR-idlerv3_left.step, CAD_RR-idlerv3_right.step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]
2023-11-01 testing release of mk2
    [CAD_RR-y_carriage_v2.step, CAD_RR-y_carriage_v2_right_mirrored.step]
2023-11-09 yolo push because i gotta switch branches
    [CAD_RR-y_carriage_v2.step, CAD_RR-y_carriage_v2_right_mirrored.step]
2024-02-14 mk2 and mk3 cad, exported parts
    [CAD_RR-Z_reprap_left.step, CAD_RR-Z_reprap_screw.step, CAD_RR-Z_reprap_v0_front.step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]
2024-02-16 update BOM for mk3
2024-02-16 update printed parts list for MK3
2024-09-10 start v2, add new assembly
    [100mmmgn_v3-Hiwin MGN9Hiwin rail MGN9R.step, 2020extrusionx.stl, 2020extrusiony.stl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]
2024-10-15 rudy v2 preparation
    [GT2_80T_5mm_Bore_Pulley.STEP]
2024-10-15 v2 BOM
2025-03-30 mk4 first batch
    [CAD_RR-YCarriage_bottom_left.step, CAD_RR-YCarriage_top_left.step, CAD_RR-belt_tensioner_left.step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]
2025-04-24 mk4 release try #0
    [CAD_RR-150_bed_carriage.step, CAD_RR-150_bed_carriage.stl, CAD_RR-2020_mgn9_mount_100mm.step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]
2025-05-24 last mk4 parts added
    [YCarriage_bottom_right.step, YCarriage_top_right.step, Z_plate.step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]
2025-06-02 mk4 goodies
    [5mm_8mm_coupler.step, Z_plate.step, bed_screw_knob.step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]
2025-06-21 CYD display option
    [5mm_8mm_coupler.step, CYD_mount.FCStd, base.step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]
2025-06-26 fix some part counts and add cad image
    [CYD_mount.FCStd, base.step, base.stl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]
